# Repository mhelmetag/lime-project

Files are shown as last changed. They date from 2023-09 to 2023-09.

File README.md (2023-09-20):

# Lime Project

A story of a repurposed rideshare e-bike.

## Intro

I found the bike on Facebook Marketplace for $100. It was a Lime bike that had been supposedly surrendered to some city in the LA area. I bought it as a project to learn more about e-bikes and to also get a cheap e-bike out of the experience.

The story seemed somewhat legit. The previous owner seemed to have around 200 Lime e-bikes. So either the story was true or he was the best Lime bike thief in the world. I'm going to assume the former.

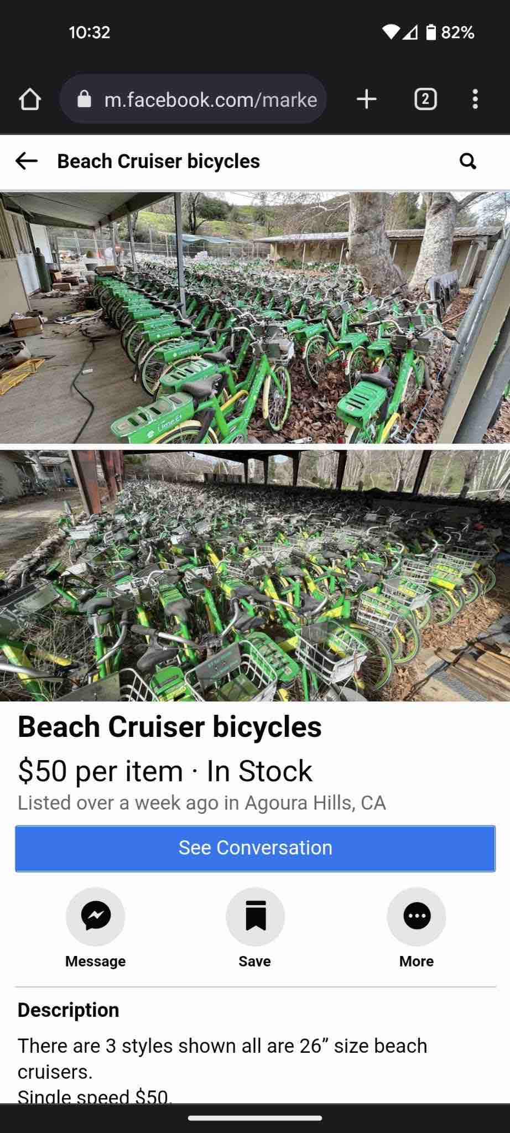
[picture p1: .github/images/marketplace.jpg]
marketplace


## The Bike

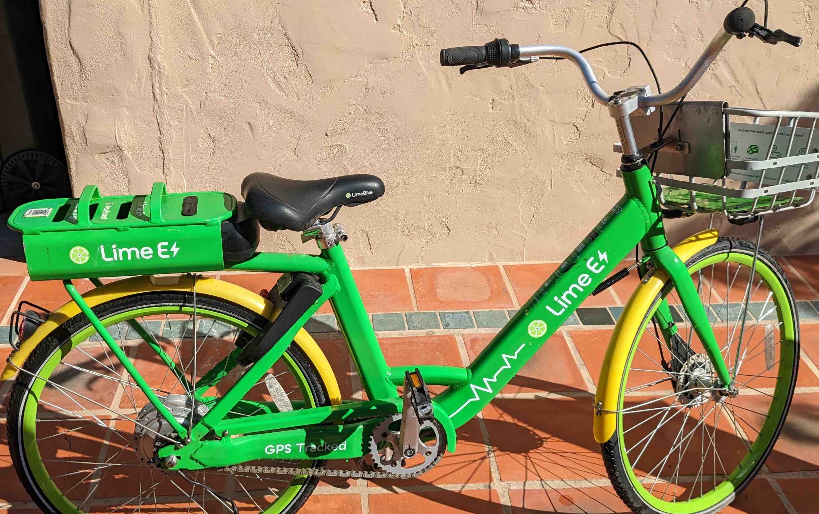
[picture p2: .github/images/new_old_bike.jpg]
new_old_bike


The bike seemed almost new. It still had some of the plastic film for packing around the crank arms and other pieces.

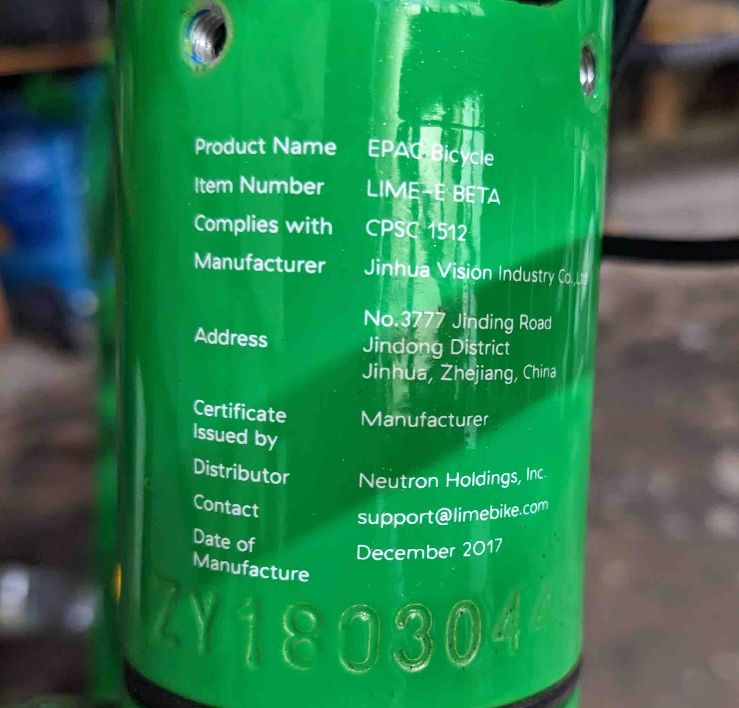
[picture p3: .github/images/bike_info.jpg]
bike_info


The bike is from 2017 and they called it the "LIME-E BETA". It has a Bafang motor (maybe 250W?), Bafang torque/cadence integrated bottom bracket and sensor, 14.5Ah 36V battery, Shimano nexus brakes, all aluminum construction (besides a a few small steel brackets) and solid tires. It's a heavy, no maintenance bike.

The main issue was that the bike was totally dead. The battery was near 0V. Even with an external power supply feeding 36V to the controller, the bike did nothing.

## Battery Revival

I ended up going against the recommendations of most of my electrically inclined friends and decided to jump start the battery. I was doing this on a budget and I thought I could get away with it by trickle charging the cells. The cells also didn't look like they were damaged or swollen in any way so it seemed mostly safe. I wouldn't recommend this but it did work for me.

For that, I opened up the battery, isolated each parallel group and used a few spare 18650 cells to boost them up until my RC charger would accept them on the li-ion setting. Once the whole battery was around 30V, I used a normal 36v li-ion charger to charge it up the rest of the way.

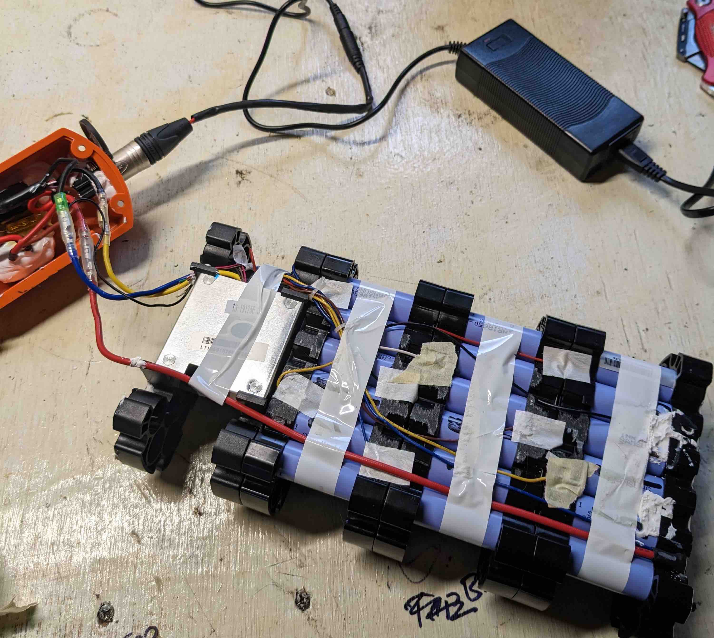
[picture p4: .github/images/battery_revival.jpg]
battery_revival


It was a bit of a pain finding the right connector for the battery. I wasn't expecting some weird connector usually used for audio devices (XLR4) but, in the end, I was able to make it work with some globs of solder and crimps.

## The Brains

Even with a fully charged battery, the bike didn't do anything. I had no idea how to turn it on. I believe the bike is supposed to turn on when the phone app sends a command to unlock and turn on the bike. My desire to have a working bike was beginning to outweigh wanting to reverse engineer how the Lime cellular chip worked with the motor controller. So in the interest of time, I bought a cheapo "KT" motor controller of eBay for about $60 all-in (4-1 connector, display and controller). If I get another chance to work on another one of these bikes, I'd probably try to figure out how that interface works so that I can keep the original motor controller.

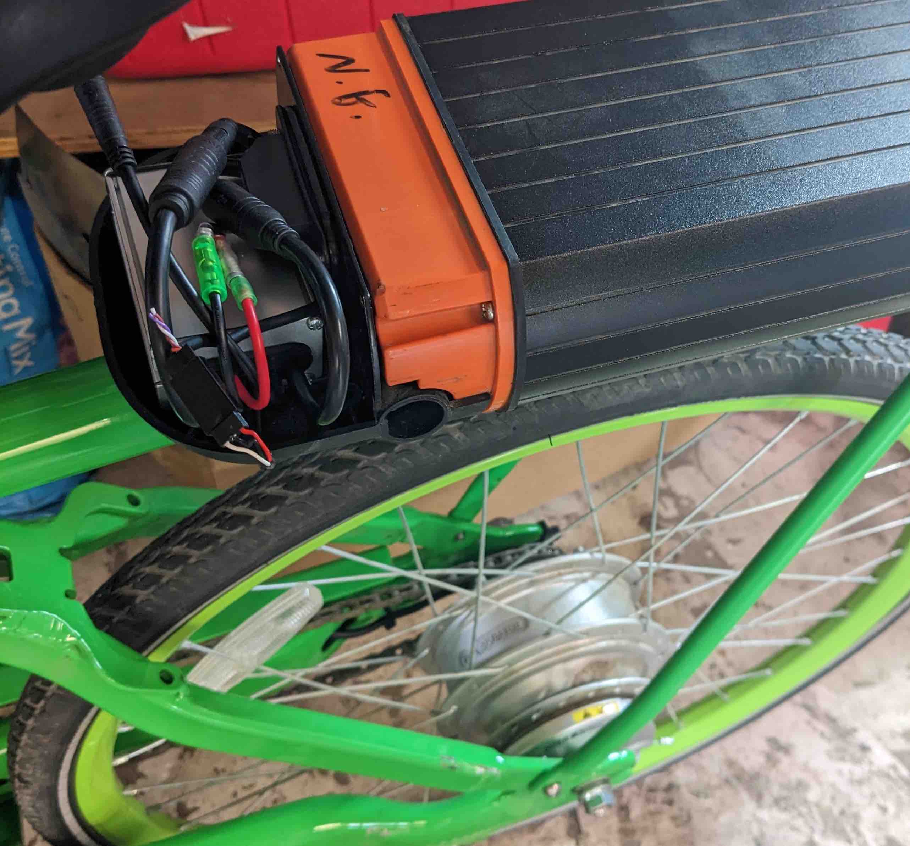
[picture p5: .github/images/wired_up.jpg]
wired_up


This new controller greatly simplified things but also lost some features of the original. The original controller supported a torque and cadence sensor. The new controller only supported cadence. The original controller had outputs for lights. The new controller didn't. One pro was that the bike no longer needed an app to turn on. I could just turn it on with the display.

## First Ride

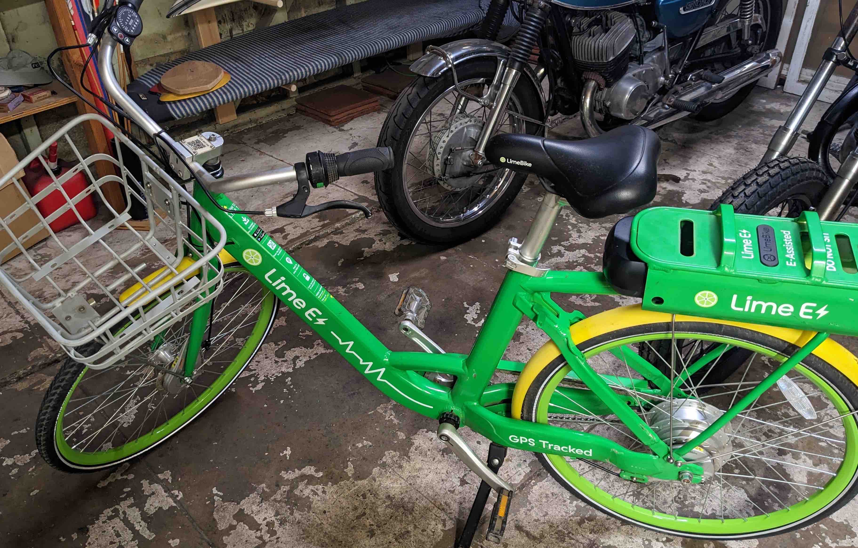
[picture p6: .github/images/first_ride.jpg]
first_ride


The bike rides pretty well! The cadence sensor is a bit wonky. It can be a bit finicky when starting but works well once you have a good rhythm. I'm not sure why but it definitely has a little to do with the sensor and controller not being exactly compatible. The controller is for a 3-pin PAS but the sensor is 6-pin. I might try to fix that in the future.

The battery isn't in the best shape. It probably has about 50% of its original capacity. When I was testing out some of the cells, they seemed to be about 50%. I get about 25 miles of range for a few hours of charging. That's plenty for me.

## NFC Lock

The last step of the project was to make the original lock work with some other kind of system. It's such a cool integrated lock. No need to carry around a big lock just to secure the bike for a few minutes during the day. For this, I chose NFC. NFC seemed like a good choice because the cards and fobs are waterproof (perfect for surfing) and they are cheap. It also would work with my phone when biking around town.

The parts list was pretty short:

- [PN532 NFC/RFID module](https://www.amazon.com/HiLetgo-Communication-Arduino-Raspberry-Android/dp/B01I1J17LC)
- [Elegoo Nano](https://www.elegoo.com/products/elegoo-nano-v3-0)

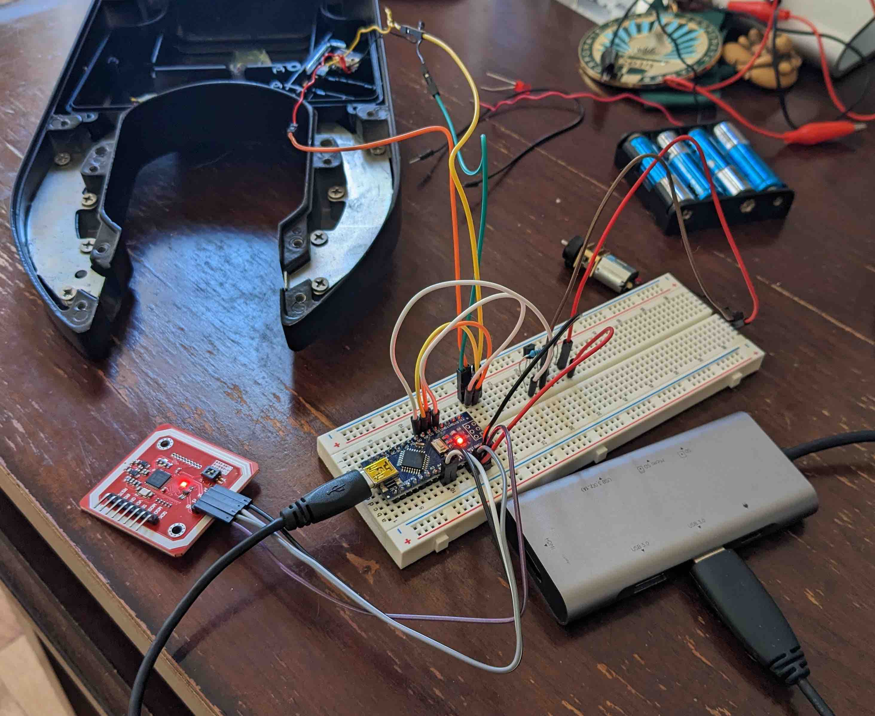
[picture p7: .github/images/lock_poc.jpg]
lock_poc


I was able to re-use most of the components of the lock (limit switches and motor for the rotating pin) but I got rid of the speaker and LEDs for simplicity.

I powered the whole set up with a 9V battery. This might bite me in the future but it was the easiest way to get it working. The Nano and PN532 are both 5V devices so I waste some power going through the Nano's voltage regulator. I also used a transistor to drive the motor directly from the battery to protect the Nano from drawing too much current. I don't have any way to tell if the 9V battery is low and it'll suck if I get locked out of my bike because the battery died. I might make a backup system in the future. And/or switch it to a rechargeable battery.

The code for the lock is in [lock.ino](lock.ino) and the NFC enclosure that I made is in [NFC Enclosure.stl](NFC%20Enclosure.stl). The NFC enclosure replaces the locks original cellular antenna enclosure. I cut off the original enclosure with a dremel and glued the new one on with hot glue.

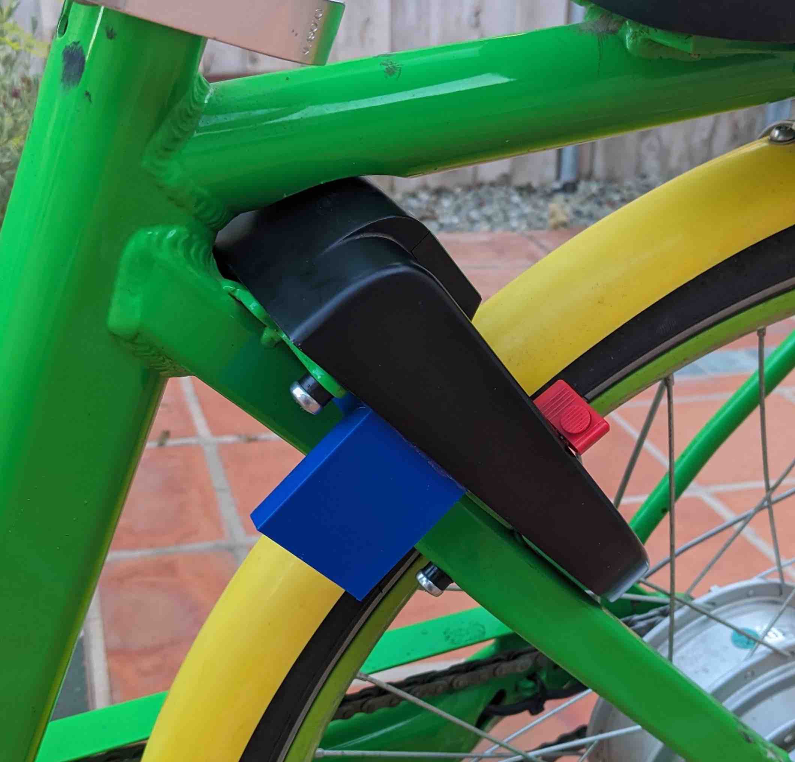
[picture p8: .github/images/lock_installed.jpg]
lock_installed


## Outro

Thanks for reading! I hope this was helpful for anyone else trying to revive a Lime bike. I'm sure more of these rideshare bikes will be available in the future as the companies go out of business, their guerilla deployments fail or they upgrade their fleets. I'm excited to see what people do with them.

I'm happy to answer any questions about the project. Feel free to email me.

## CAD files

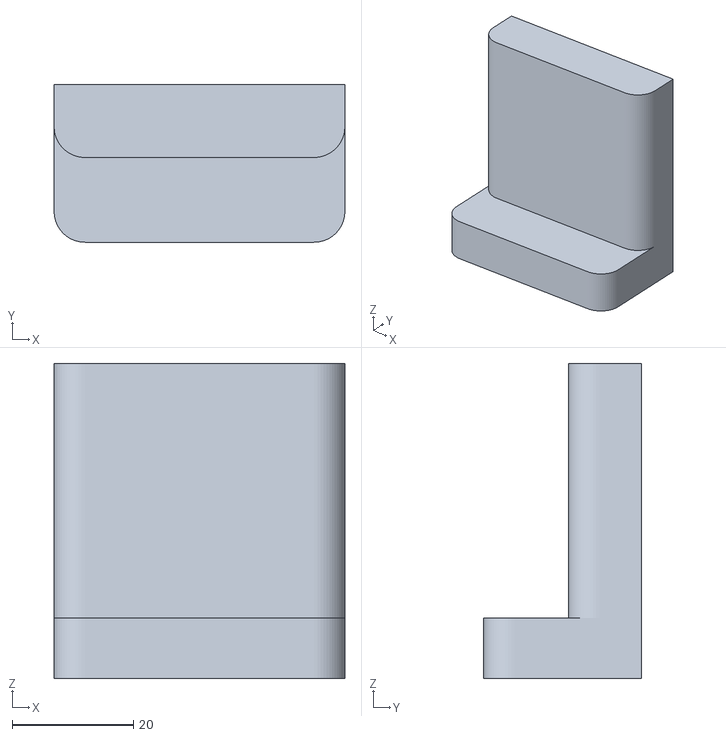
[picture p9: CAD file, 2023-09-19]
NFC Enclosure.stl
48.0 x 26.0 x 52.0

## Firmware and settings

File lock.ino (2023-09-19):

#include <ezButton.h>

#include <Wire.h>
#include <PN532_I2C.h>
#include <PN532.h>
#include <NfcAdapter.h>

// Switches
ezButton lockedSwitch(2);
ezButton unlockingSwitch(3);

// NFC config
PN532_I2C pn532i2c(Wire);
PN532 nfc(pn532i2c);

// Motor
int motorPin = 4;

void setup() {
  Serial.begin(115200);
  Serial.println("Fancy Lock V0.3");

  // Switch setup
  lockedSwitch.setDebounceTime(50);

  // NFC setup
  nfc.begin();
  nfc.setPassiveActivationRetries(0xFF);
  nfc.SAMConfig();

  // Motor
  pinMode(motorPin, OUTPUT);
}

void loop() {
  // NFC state
  // Valid NFC card data
  uint8_t validUid[] = { 131, 182, 44, 146, 0, 0, 0 };

  // State for NFC reading
  boolean success;
  uint8_t uid[] = { 0, 0, 0, 0, 0, 0, 0 };  // Buffer to store the returned UID
  uint8_t uidLength;                        // Length of the UID (4 or 7 bytes depending on ISO14443A card type)

  // State for NFC matching
  boolean match;

  if(lockedSwitch.getStateRaw() == LOW) {
    Serial.println("Locked!");

    success = nfc.readPassiveTargetID(PN532_MIFARE_ISO14443A, &uid[0], &uidLength);
    if (success) {
      Serial.println("Card read!");

      match = true;
      for (uint8_t i=0; i < 4; i++) {
        if (validUid[i] != uid[i]) {
          match = false;
          break;
        }
      }

      if (match) {
        Serial.println("Card match!");

        Serial.println("Unlocking in 3 seconds!");
        delay(3000);

        Serial.println("Unlocking...");
        digitalWrite(motorPin, HIGH);
        
        boolean unlocking = true;
        while (unlocking) {
          unlockingSwitch.loop();

          if (unlockingSwitch.isReleased()) {
            digitalWrite(motorPin, LOW);
            unlocking = false;
          }
        }
        
        Serial.println("Unlocked!");
        delay(3000);
      } else {
        Serial.println("Card mismatch!");
      }
    }
  }
}
